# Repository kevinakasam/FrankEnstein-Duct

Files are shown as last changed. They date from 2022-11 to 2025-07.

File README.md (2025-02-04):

## Welcome to the release version of the FrankEnstein V2 Toolhead!

As the brainchild of KevinAKASam and successor to the orginal Frank toolhead, Frank 2 builds upon it's predecessor by being even more modular with support for a wide vareity of hotends and extruders for the Ender 3 and similar with its carriage plate mount as well as as any printer with a front MGN12H linear rail (with some tweaking depending on the printer). Frank 2 features double sided dual fan cooling for either 4010 or 5015 blower fans and well as the option of either 3010 or 4010 fans (with printed adapter) for hotend cooling. The entire tool head is held together securely by 4 screws to the mount and 2 from the extruder mount for easy assembly and disassembly. As in Frank 1, Frank 2 also uses standard Voron spec heat set inserts (M3x5x4) to ensure the longevity of your printed parts while assembling and dissaembling.

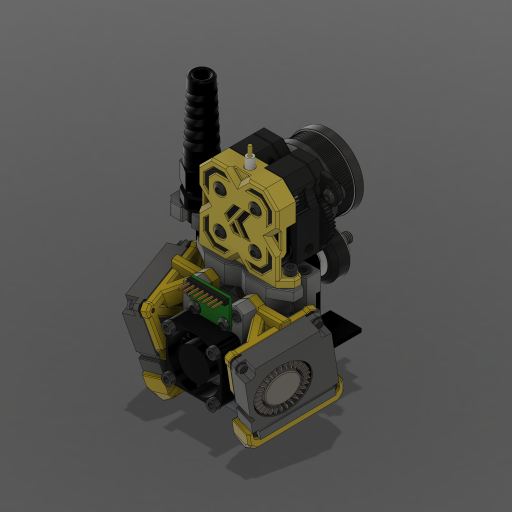
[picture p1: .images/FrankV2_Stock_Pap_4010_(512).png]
Frank V2 using the stock Ender hotend with the Papilio Lite, dual 4010 part cooling, and 3010 hotend cooling


<dl>
<dt>Supported Hotends:</dt>
<dd>Dragon</dd>
<dd>Dragonfly BMO</dd>
<dd>Dragonfly BMS (7 fin)</dd>
<dd>Spider Pro</dd>
<dd>Spider V2</dd>
<dd>Stock Ender 3 (Creality Mk8)</dd>
<dd>Triangle Labs TR6</dd>
<dd>TZ V6</dd>
<dd><em>and most hotends that use one of the above mounting patterns...</em></dd>

<dt>Supported Extruders:</dt>
<dd>Bowden</dd>
<dd>LGX Lite</dd>
<dd>Orbiter 1.5</dd>
<dd>Orbiter 2.0</dd>
<dd>Papilio</dd>
<dd>Sherpa Mini (with or without K Face)</dd>
<dd><em>and most extruders that use one of the above mounting patterns...</em></dd>
</dl>

#### Bill of Materials

| Item 					| Quantity | |
|---|---|---|
| **For Carriage Plate Base:** 					| | |
| &nbsp;&nbsp;Voron spec heatset insert 		| x6 (x7 for E3 V2 plate) | |
| &nbsp;&nbsp;M3x8 SHCS 		| x2 | |
| &nbsp;&nbsp;**For BL/CR Touch Mount:** 	| | |
| &nbsp;&nbsp;&nbsp;&nbsp;M2x8mm SHCS | x2 | |
| 					| | |
| **For MGN12H Base:** 					| | |
| &nbsp;&nbsp;300mm MGN12H Linear Rail 		| x1 | |
| &nbsp;&nbsp;Voron spec heatset insert 		| x10 | |
| &nbsp;&nbsp;M3x4mm or 5mm SHCS 		| x4 | |
| &nbsp;&nbsp;M3x35mm BHCS (preferred) or SHCS		| x2 | |
| &nbsp;&nbsp;**For Cable mount:** 		| | |
| &nbsp;&nbsp;&nbsp;&nbsp;M3x10mm SHCS | x2 | |
| &nbsp;&nbsp;**For Klack Mount:** 		| | |
| &nbsp;&nbsp;&nbsp;&nbsp;M3x6mm SHCS | x2 | |
| 					| | |
| **For Hotend Mount:** 					| | |
| &nbsp;&nbsp;Hotend of choice 		| x1 | |
| &nbsp;&nbsp;Voron spec heatset insert 		| x8 (or x10 for some hotends) | |
| &nbsp;&nbsp;Hotend mounting screws 		| Varies (Should come with hotend)| |
| &nbsp;&nbsp;M3x35mm SHCS 	 | x4 | |
| &nbsp;&nbsp;**For 3010 and 4010 Cooling:** 		| | |
| &nbsp;&nbsp;&nbsp;&nbsp;3010 or 4010 axial fan	| x1 (Ball bearing preferred)	  | |
| &nbsp;&nbsp;&nbsp;&nbsp;M3x12mm SHCS | x4 | |
| &nbsp;&nbsp;**For 4010 fan adapter:** 		| | |
| &nbsp;&nbsp;&nbsp;&nbsp;M3x8mm SHCS | x4 | |
| &nbsp;&nbsp;&nbsp;&nbsp;Voron spec heatset insert | x4 | |
| 					| | |
| **For Extruder Mount:** 					| | |
| &nbsp;&nbsp;Extruder of choice 		| x1 | |
| &nbsp;&nbsp;Voron spec heatset insert 		| x2 to x4 depending on extruder  | |
| &nbsp;&nbsp;M3x20mm SHCS or BHCS or 		| x2 (non-LGX Lite) | |
| &nbsp;&nbsp;M3x8mm SHCD or BHCS 		| x2 (LGX Lite ONLY) | |
| &nbsp;&nbsp;Extruder mounting screws 		| Varies (Mostly some amount of M3x6/8/10mms)| |
| 					| | |
| **For Part Cooling:** 					| | |
| &nbsp;&nbsp;**For Dual 4010:** 		| | |
| &nbsp;&nbsp;&nbsp;&nbsp;4010 blower fan | x2 | |
| &nbsp;&nbsp;&nbsp;&nbsp;M2x8mm SHCS | x6 | |
| &nbsp;&nbsp;&nbsp;&nbsp;M2x10mm SHCS | x2 | |
| &nbsp;&nbsp;&nbsp;&nbsp;M2 Washer | x2 | |
| &nbsp;&nbsp;**For Dual 5015:** 		| | |
| &nbsp;&nbsp;&nbsp;&nbsp;5015 blower fan | x2 | |
| &nbsp;&nbsp;&nbsp;&nbsp;Voron spec heatset insert | x6 | |
| &nbsp;&nbsp;&nbsp;&nbsp;M3x8mm SHCS | x2 | |
| &nbsp;&nbsp;&nbsp;&nbsp;M3x20mm SHCS | x4 | |
| &nbsp;&nbsp;&nbsp;&nbsp;M3 Washer | x4 | |

#### Print Settings: The Magic 5

```
Infill:
* 55%
Walls/Perimeters:
* 5
Top Layers:
* 5
Bottom Layers:
* 5
```

Not finding exactly what you need? Check out [User Mods](./User_Mods) to see if it's been made or if it hasn't feel free to design it and request a pull in User Mods!

Have a question or just want to hang out with some cool people? [Join our discord here!](https://discord.gg/xqpKrxt9FC)

_Build guide coming..._

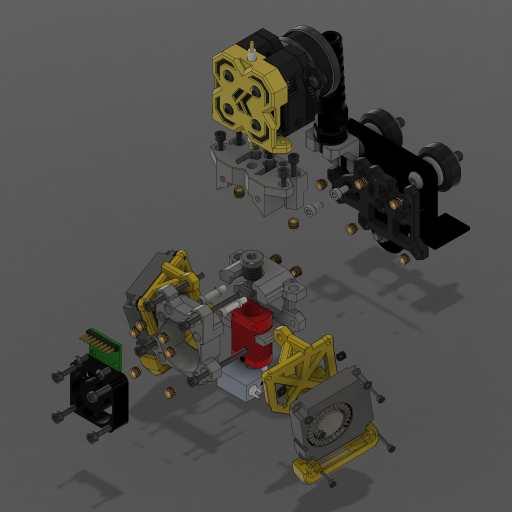
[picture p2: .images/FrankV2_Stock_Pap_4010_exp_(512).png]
An exploded view of the above Frank


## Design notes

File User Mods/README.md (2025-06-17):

# User Mods

This repository is to share your Mods (Mods of my Mods are called Mods in the following). You can add them by submitting a pull request.
All my Mods have a sperate folder, that may include further subfolders, please sort your content as described below:

## Table structure

*Thanks to the [Voron_User](https://github.com/VoronDesign/VoronUsers) Repo for this table schematic! 
Update the following table with the information about your mod:
- Your name
- A link to your sub-folder
- A short description of your mod

like so:
`
| Creator | [Mod title](link) | Description | :x: | :x: |`

| Creator | Mod title | Description |
| --- | --- | --- |
| adamstorm | [Filament Sensor](<./adamstorm/Filament Sensor>)| A simple filament sensor in the extruder mount for Papilio/Sherpa mounting pattern extruders |
| | [Camera Mount](<./adamstorm/Camera Mount>)| Add a nozzle camera to your Ender! |
|			| [Sprite Extruder Mount](<./adamstorm/Sprite Extruder Mount>)| Extruder mount for the Creality Sprite extruder |
| wight554 | [2510 Fan Dragon Mount](<./wight554/2510 Fan Dragon Mount>)| Hotend mount using 2510 fan for Dragon mount hotends |
| | [5015 HF Ducts](<./wight554/5015 HF Ducts>)| 5015 fan ducts for "HF sized" hotends |
| | [5015 UHF Ducts](<./wight554/5015 UHF Ducts>)| 5015 fan ducts for "UHF sized" hotends |
| | [Extruder Mounts](<./wight554/Extruder Mounts>)| A bunch of alternative extruder mounts |
| | [Klack HF](<./wight554/Klack HF>)| Klack dock and mount for "HF sized" hotends |
| | [Klack UHF](<./wight554/Klack UHF>)| Klack dock and mount for "UHF sized" hotends |
| | [PG7 Mount](<./wight554/PG7 Mount>)| PG7 Mount that's designed to be a bit more rigid |
| n4t3y | [AIO 5015 Duct](<./n4t3y/AIO 5015 Ducts>) | A mount for the 5015 fans with integrated duct instead of separately fixed |
| | [AIO 5015 LED Duct](<./n4t3y/AIO 5015 LED Ducts>) | A mount for the 5015 fans with integrated duct and LED Mount instead of separately fixed |
| SampleMan | [Sample](./SampleMan/Sample) | This is a sample entry |

## How to create a pull request 

1. Create a fork of the repository
    - You can find a Button labeled `Fork` at the top right. Clinking on that creates a copy aka fork of this respository in your GitHub account.

2. Create a new folder
    - Navigate into the Mod folder you want to upload your Mod to.
    - Click on `Add file` -> `Create new file`. Then type `YourNickname/YourModName/README.md` to create your folder (click on `commit new file`).
    - If you plan to upload more than one Mod, add simply add more subfolders in your folder like `YourNickname/YourFirstModName/README.md` and `YourNickname/YourSecondModName/README.md` and so on. 
    - Please use short folder names.

3. Edit README and add your files
    - Click on the README.md and then on the pencil on the right top/center to edit the README. Add all required information as described below.
    - Click on `Add file` -> `Upload files` to upload all your Mod files.
    - The stock title of a commit is `Add files via upload` replace that with the title of your Mod.

4. Edit the main README.md of the Mod
    - Navigate back to the Mod folder you made your Mod for. Edit this file and add your mod to the alphabetic table by adding a new line with `| Creator | [Mod title](link) | Description | | :x: | :x: |`
    - The `link` for the `[Mod title](link)` should look like that: `./YourNickname/YourModName` just like you did above
    - Example: `| KevinAkaSam | [Modifius](./KevinAkaSam/Modifius) | Modifius adds ...  | :grey_question: | :grey_question: |`
    - Note `Modifius` is just an idea, yours may be called `Adaption to bearing size xy`

5. Submit the Pull Request
    - Navigate back to this repository (not the one you forked) and click on `Pull requests` next to `<> Code` `© Issues`
    - Click on the green square on the right `New pull request`
    - A new dialog/window opens and starts with:
        >Compare changes
        >
        >Compare changes across branches, commits, tags, and more below. If you need to, you can also `compare across forks`.
    - Click on the `compare across forks` and at the line below select your forked respository as `head respository`
    - Add you Mod name as title of the pull request, add the information to the form and click on  `Create Pull Request` at the very end.
    - If you did anything right we will merge your pull request :)
 
## Create a folder

To add your work create a folder that has the following structure:

    - Main repository `User-Mods` 
        - Nickname Subfolder eg. `KevinAkaSam`
            - Modname Subfolder eg. `Modifius`
            - Modname Subfolder eg. `Modimedi`
        - Nickname Subfolder eg. `hawk16zz`
            - Modname Subfolder eg. `Mod_A`
            - Modname Subfolder eg. `Mod_B`

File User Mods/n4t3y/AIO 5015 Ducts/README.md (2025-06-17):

This mod combines the 5015 holder and duct into a single piece to aid with duct drooping and fitment to the fan, while also removing a heat insert and bolt which would otherwise be needed for attaching the duct to the mount. An integrated wedge support piece is included to remove the need for adding slicer generated supports.

The model is fully printable without supports, although the top side of the duct can come out stringy but will still work fine after removing the hanging filament.

The LHS is the base printable file and to print the RHS, the mount and bracket should be mirrored in the slicer.

The mount is designed to be oriented in the slicer like this (grey element is integrated support):

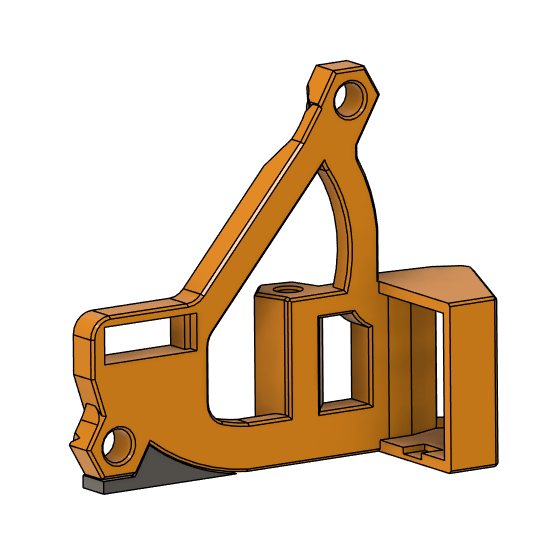
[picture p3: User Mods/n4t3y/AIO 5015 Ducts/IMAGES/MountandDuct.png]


The bracket is held in place with a notch integrated into the mount, as well as the fan when it is installed, so there is no need for any additional hardware.

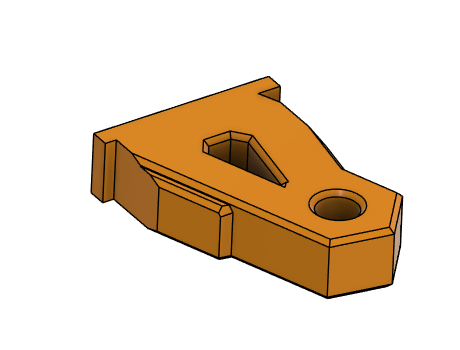
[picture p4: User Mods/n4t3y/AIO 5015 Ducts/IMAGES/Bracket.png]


The bracket should slide easily into the slot in the mount (take note of orientation of bracket in the mount):

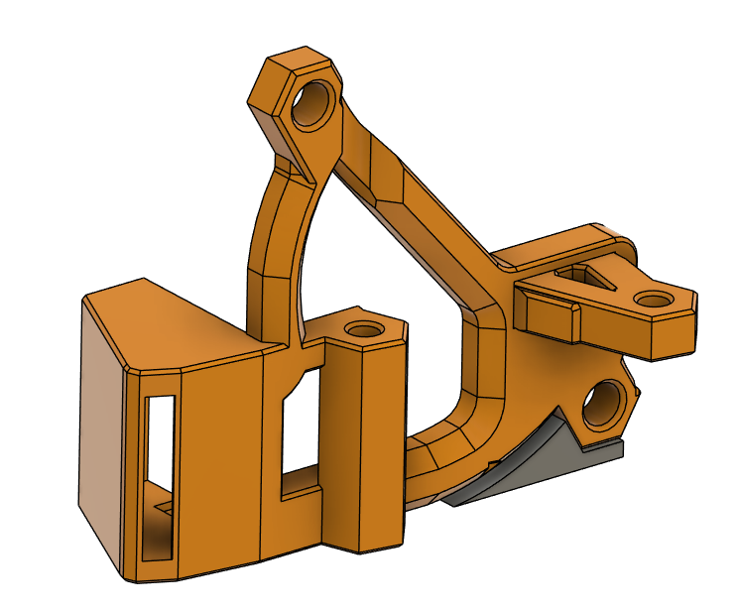
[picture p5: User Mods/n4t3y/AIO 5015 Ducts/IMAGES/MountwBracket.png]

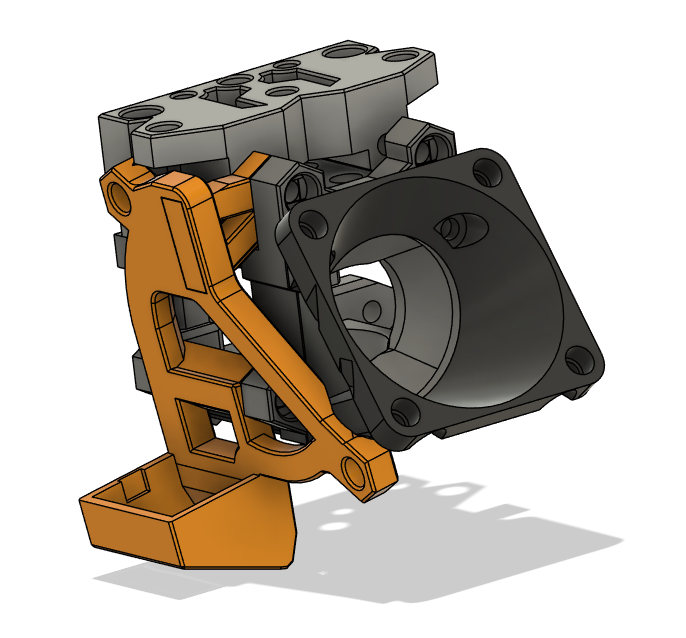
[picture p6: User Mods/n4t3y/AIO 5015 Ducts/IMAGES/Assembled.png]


The additional material around the bracket may intrude a bit on the intake of the fan on the right hand side, but not a significant amount more than the original holder.

Original Holder:

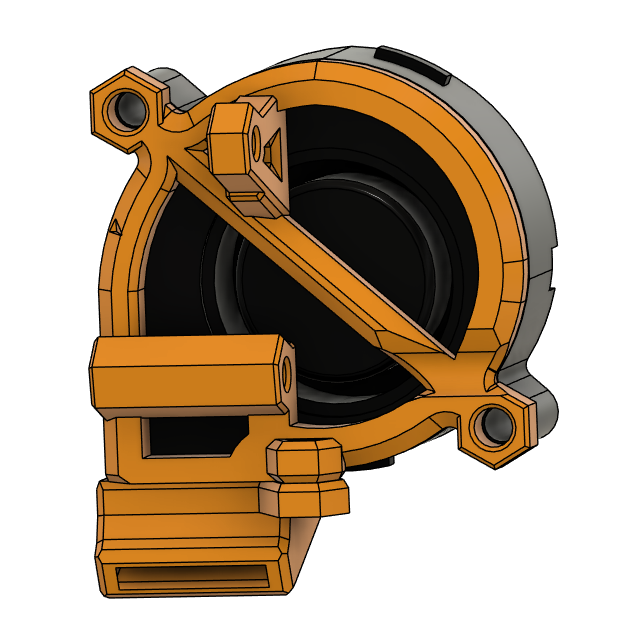
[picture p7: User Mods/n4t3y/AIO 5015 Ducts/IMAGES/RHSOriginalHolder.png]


AIO Mount:

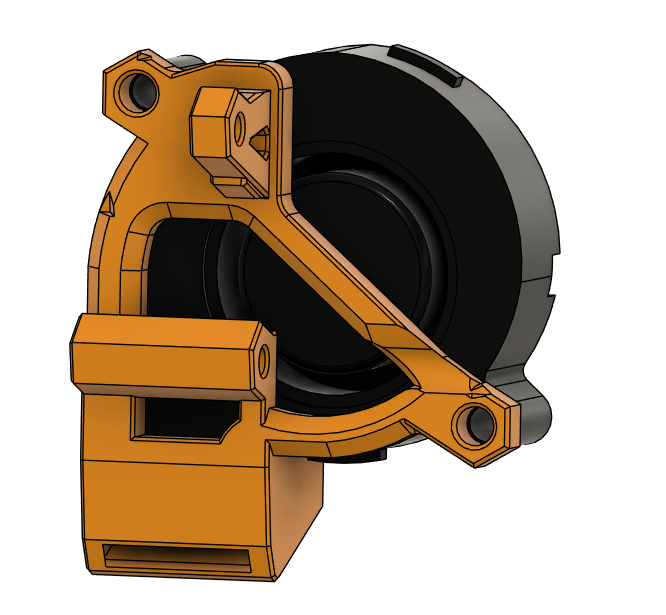
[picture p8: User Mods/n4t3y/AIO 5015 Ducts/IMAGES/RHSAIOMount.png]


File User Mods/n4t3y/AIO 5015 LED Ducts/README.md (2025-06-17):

This mod adds LED holders to the AIO 5015 duct. It is compatible with the same wedge support in the base duct.

The model is fully printable without supports, although the top side of the duct can come out stringy but will still work fine after removing the hanging filament.

The LHS is the base printable file and to print the RHS, the mount and bracket should be mirrored in the slicer.

Orientation is the same as the base AIO Duct. Refer to the base AIO instructions [here](../AIO%205015%20Ducts/README.md) for printing instructions.

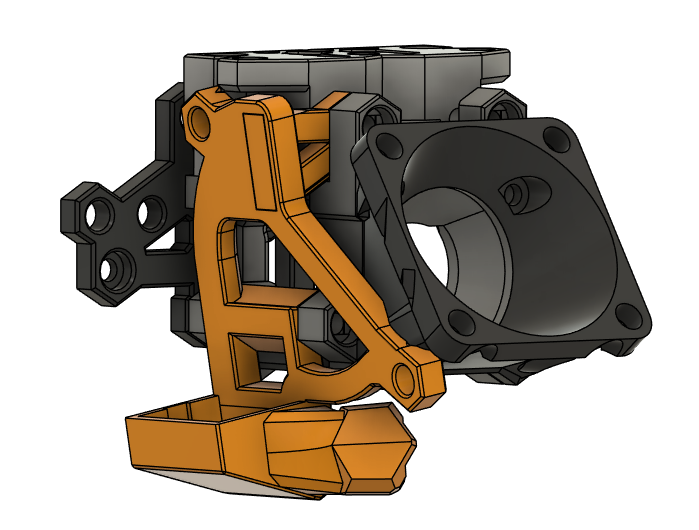
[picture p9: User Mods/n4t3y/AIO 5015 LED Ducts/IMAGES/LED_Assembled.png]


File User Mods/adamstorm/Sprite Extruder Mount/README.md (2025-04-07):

The Creality Sprite Extruder is a common upgrade/stock option that many Ender users have. While there are better extruders out there, it is a capable extruder. Just a little heavy. I don't judge ;-) 

In the interest of working with what you have, I created this mount. The Sprite extruder was the first upgrade I made on my Ender, but I quickly found that I wanted to upgrade the part cooling capability. Frank fit the bill but didn't support my only DD extruder at the time. 

STL is oriented for proper printing, no supports needed. CAD is included for your remixing pleasure. 

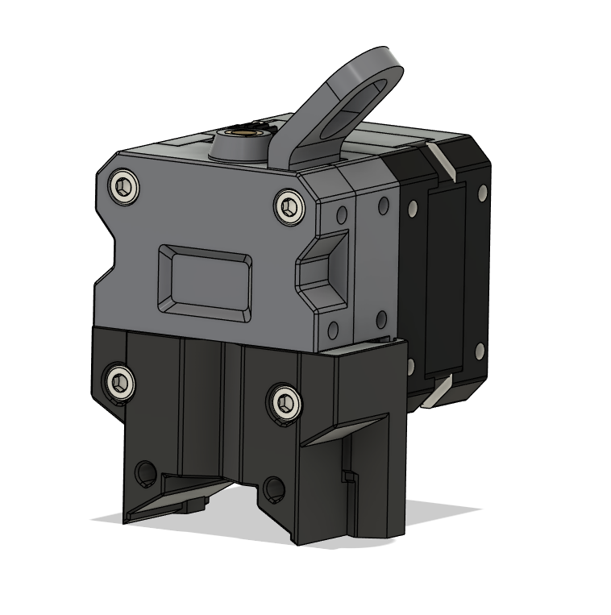
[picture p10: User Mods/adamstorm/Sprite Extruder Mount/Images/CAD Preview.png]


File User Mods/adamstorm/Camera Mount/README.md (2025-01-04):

Add a nozzle camera to your Ender!
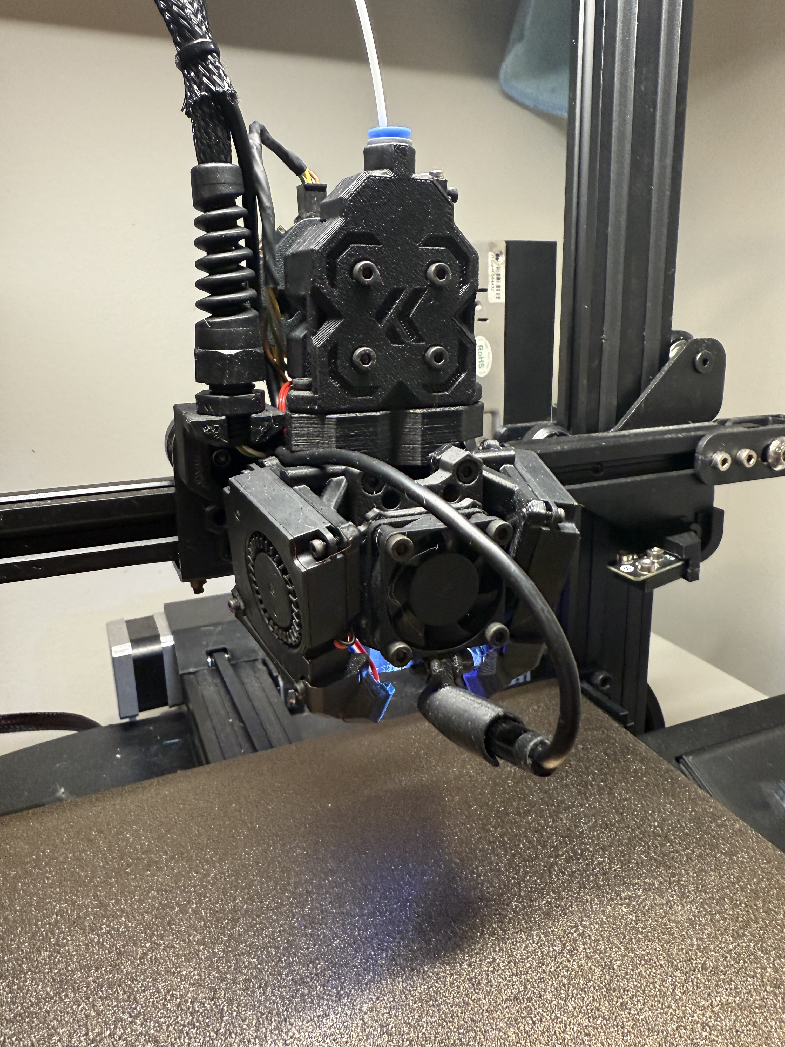
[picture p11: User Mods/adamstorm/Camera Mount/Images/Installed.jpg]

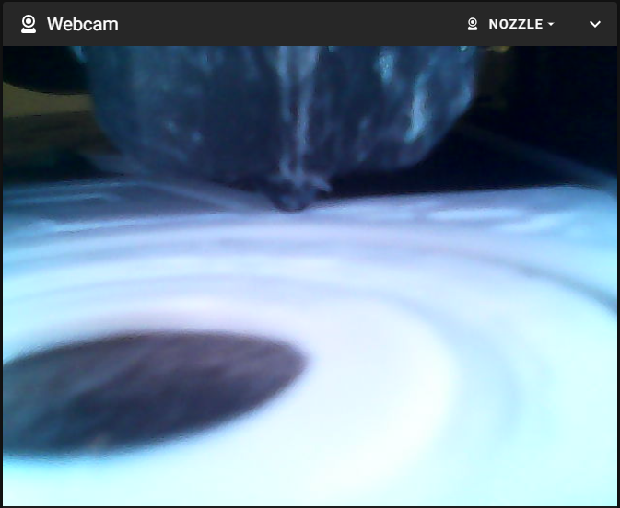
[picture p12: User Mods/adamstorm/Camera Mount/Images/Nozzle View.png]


I picked up a cheap endoscope off Temu and needed a way to mount it. This is a plate that is sandwiched between the hotend mount and 3010 fan or 4010 adapter. It gives a simple mounting point to add your favorite accessory. All you need is an M3 bolt and M3 nut. The screws that mount your 3010 fan or 4010 adapter might need to be a tad bit longer.

The included camera mount is for an endoscope that is 7.4mm in diameter. It is held in with a friction fit, the cutout portion allows for tight fit by flexing to accomodate the camera. CAD file is included if you want to modify for other size camera or other accessory.

STLs are oriented for how I printed the parts. For strength, I printed the camera mount on it's end. It printed fine for me, but it does have a small bed contact area so it might test your bed adhesion. I can see some setups would need to enable a brim in the slicer, but it did print successfully for me without. YMMV.

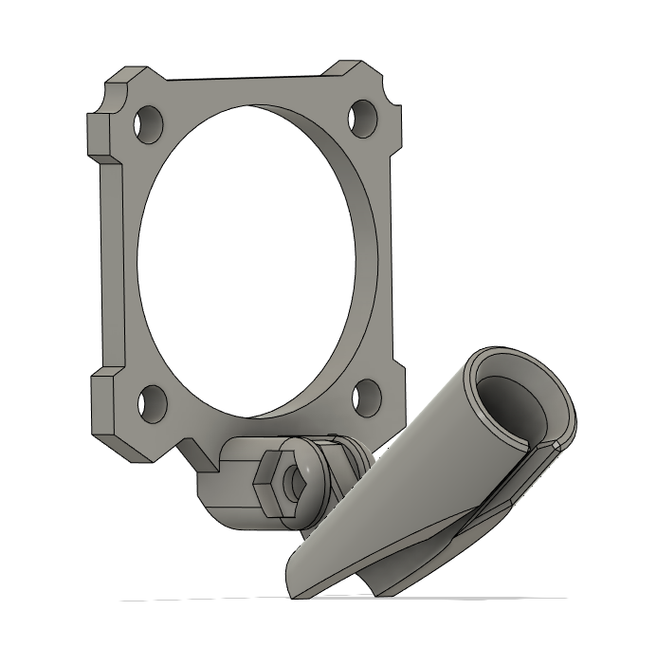
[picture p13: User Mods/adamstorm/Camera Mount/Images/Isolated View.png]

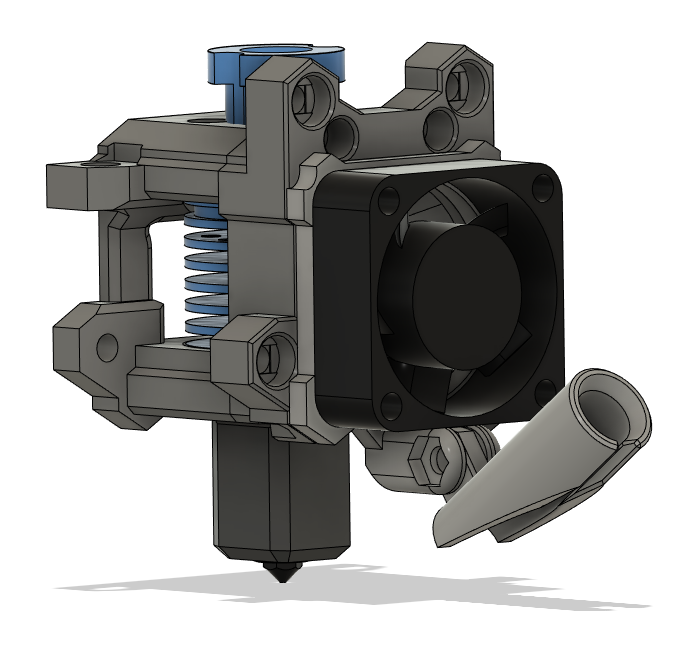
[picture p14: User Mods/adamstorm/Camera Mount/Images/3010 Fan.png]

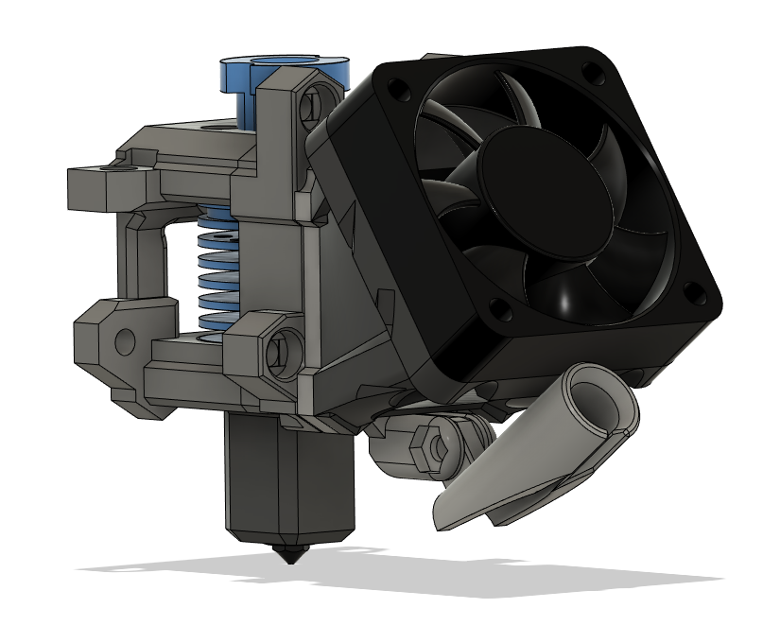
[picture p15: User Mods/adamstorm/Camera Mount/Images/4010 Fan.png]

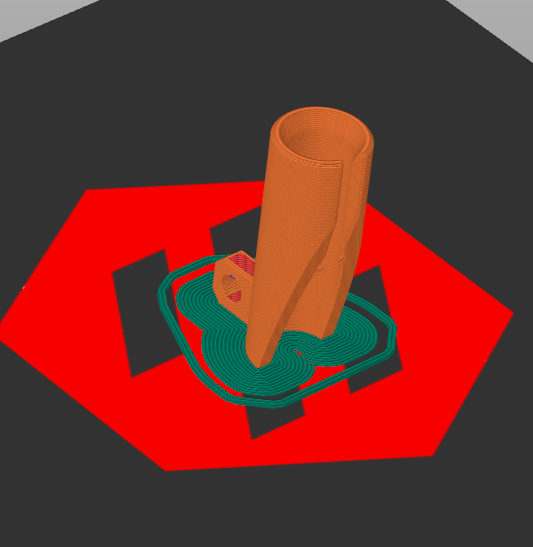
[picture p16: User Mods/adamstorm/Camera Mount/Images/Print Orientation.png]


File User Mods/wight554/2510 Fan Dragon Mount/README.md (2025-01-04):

## 2510 Fan Mount for Dragon mount hotends

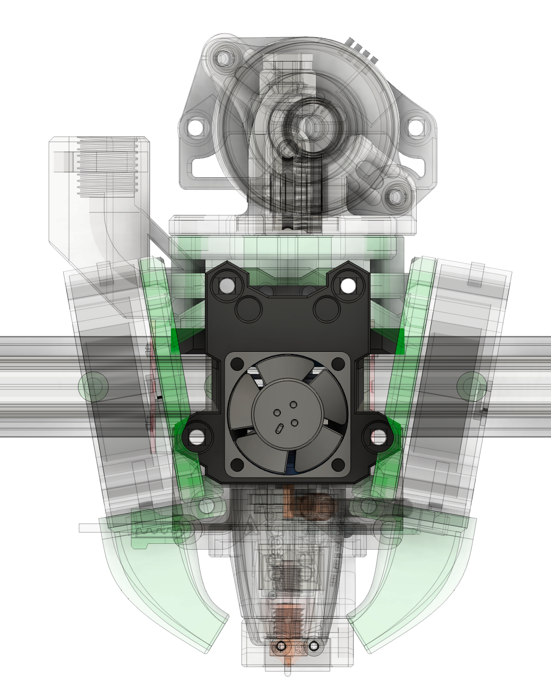
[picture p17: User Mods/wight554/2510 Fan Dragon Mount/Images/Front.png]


### Description

2510 tend to be less prone to clog on Dragons and similar hotends, so it's a nice upgrade to have on Frank

### BOM

- 4x M2.5X14mm screws (16mm should work too)
- 2510 Fan (Delta Electronics 5v ASB02505SHA-AY6B preferred)

### Assembly

Should be the same as 3010 version, I made assembly somewhat easier but it should be straightforward anyway.

### Delta 5v installation guide (for EBB36/42) borrowed from Replimat labs:

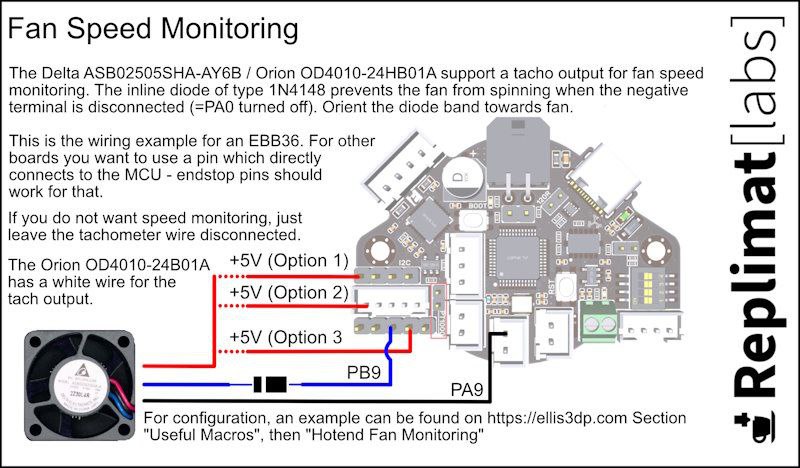
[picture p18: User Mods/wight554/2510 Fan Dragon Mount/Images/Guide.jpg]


### Other Images:

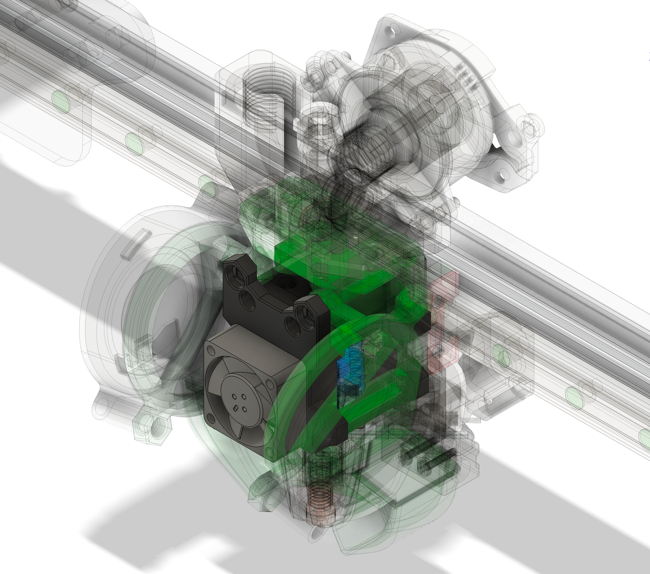
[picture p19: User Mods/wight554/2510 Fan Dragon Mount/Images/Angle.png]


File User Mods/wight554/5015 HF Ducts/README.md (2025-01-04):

## 5015 HF Ducts

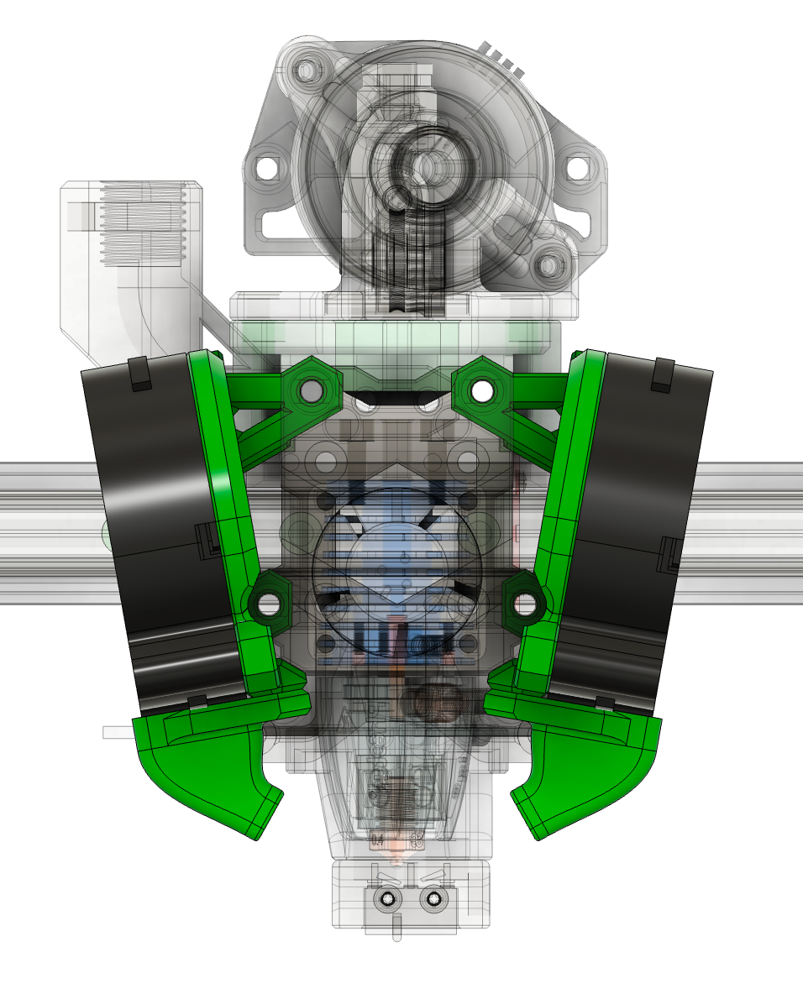
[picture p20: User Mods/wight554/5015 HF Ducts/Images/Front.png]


### Description

Longer ducts inspired by LH Stinger to work with volcano (or 8.5mm longer) versions of supported hotends and others, like Rapido HF

### BOM

The same as normal ducts

### Assembly

The same as normal ducts

### Other Images:

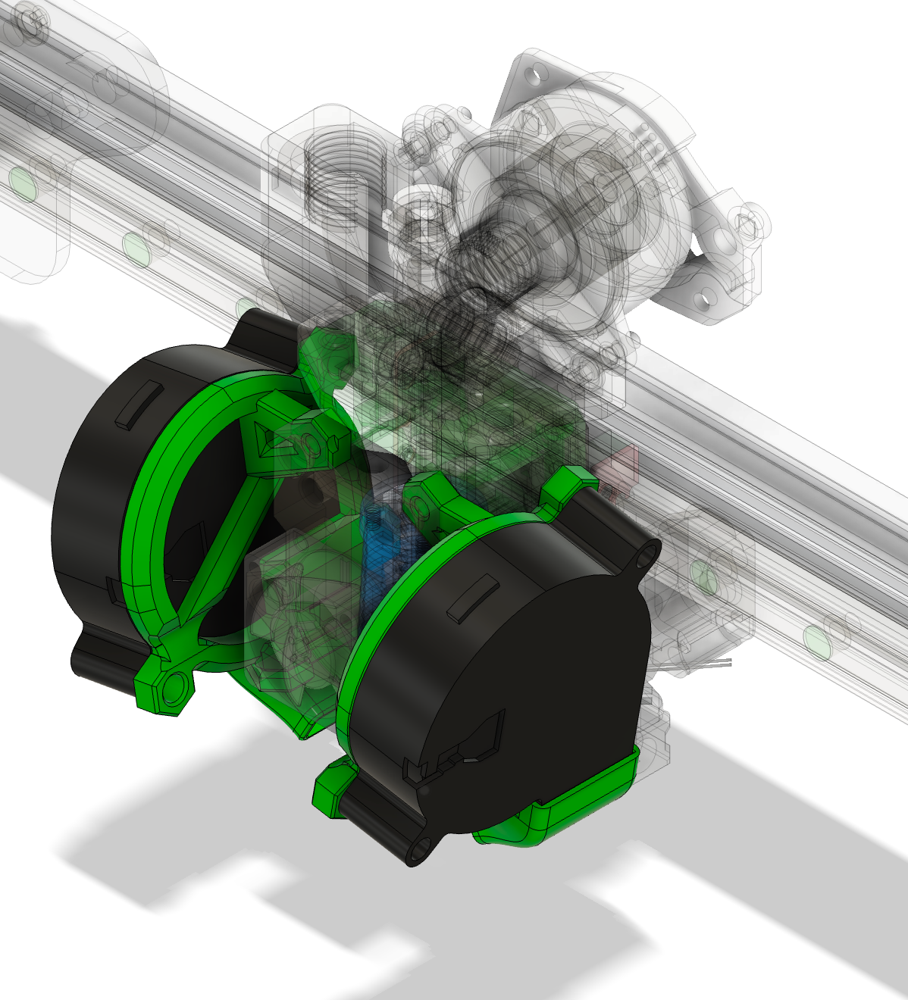
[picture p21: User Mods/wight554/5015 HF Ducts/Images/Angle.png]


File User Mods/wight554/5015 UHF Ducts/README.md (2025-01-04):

## 5015 UHF Ducts

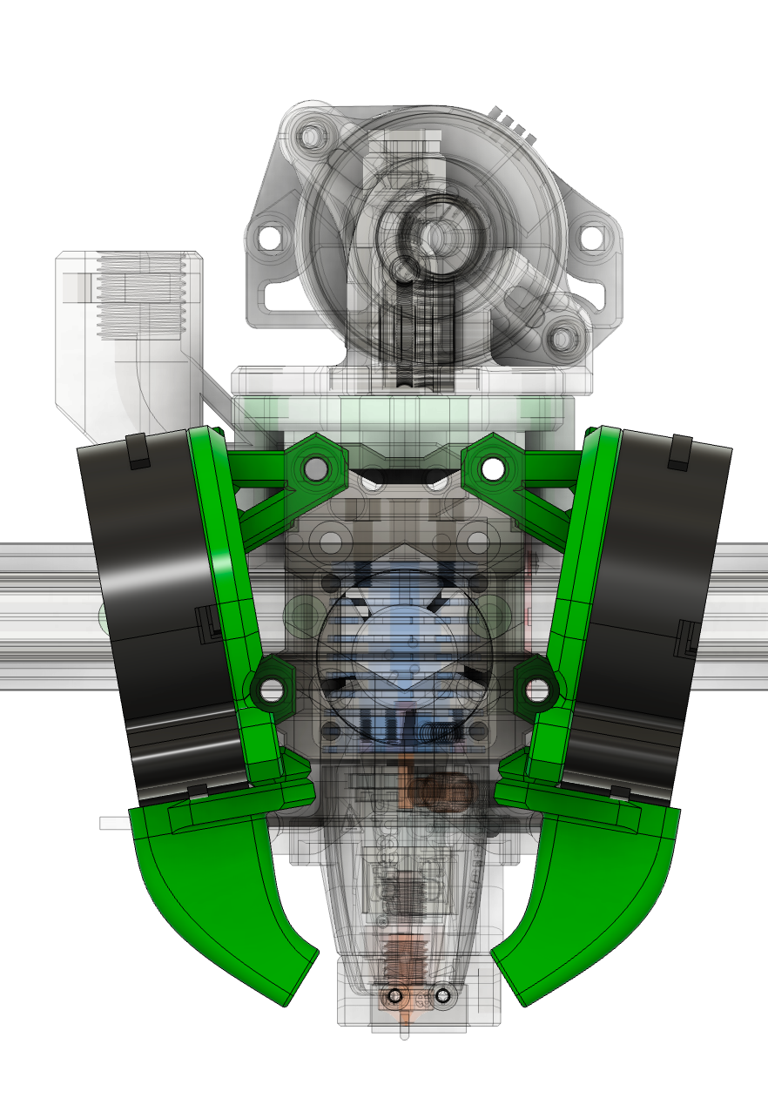
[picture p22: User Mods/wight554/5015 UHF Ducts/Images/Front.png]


### Description

Longer ducts inspired by LH Stinger to work with supported hotends with long meltzone (17mm longer than Dragon and similar) and others, like Rapido UHF

### BOM

The same as normal ducts

### Assembly

The same as normal ducts

### Other Images:

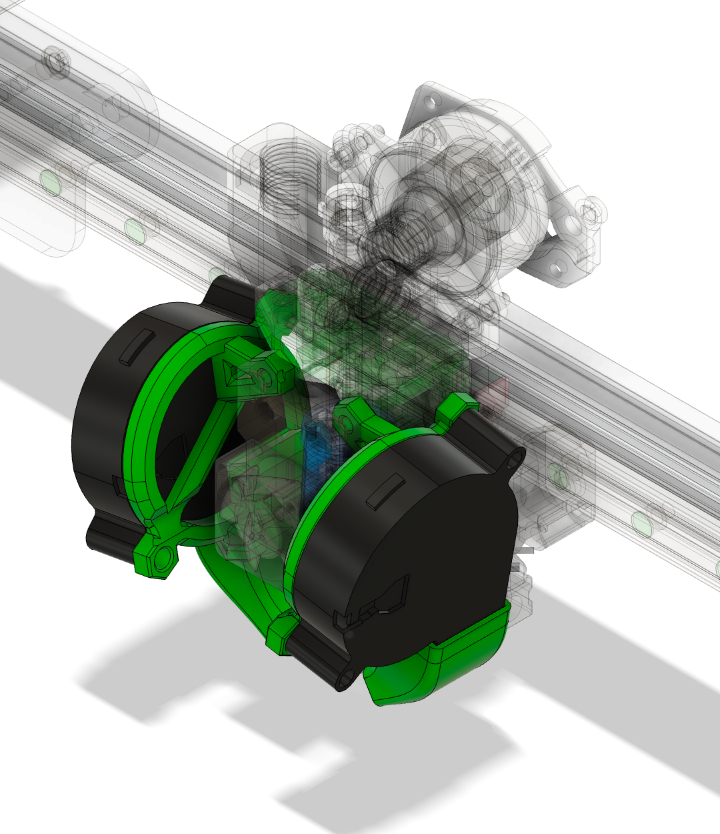
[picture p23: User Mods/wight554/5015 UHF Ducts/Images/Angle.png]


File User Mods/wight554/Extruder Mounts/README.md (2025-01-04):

## Extruder Mounts

### Description

Assortment of extruder mounts I made with some minor improvements:

- LowBoi (Orbiter mount)
- Papilio Lite (3 screw, alternative mount using a nut at rear)
- WWMBG (Orbiter mount)
- Protoxtruder 2

### BOM

Same as normal, except M3 Hexnut for Papilio Lite mount

### Printing

Designed to be printed laying on this face:
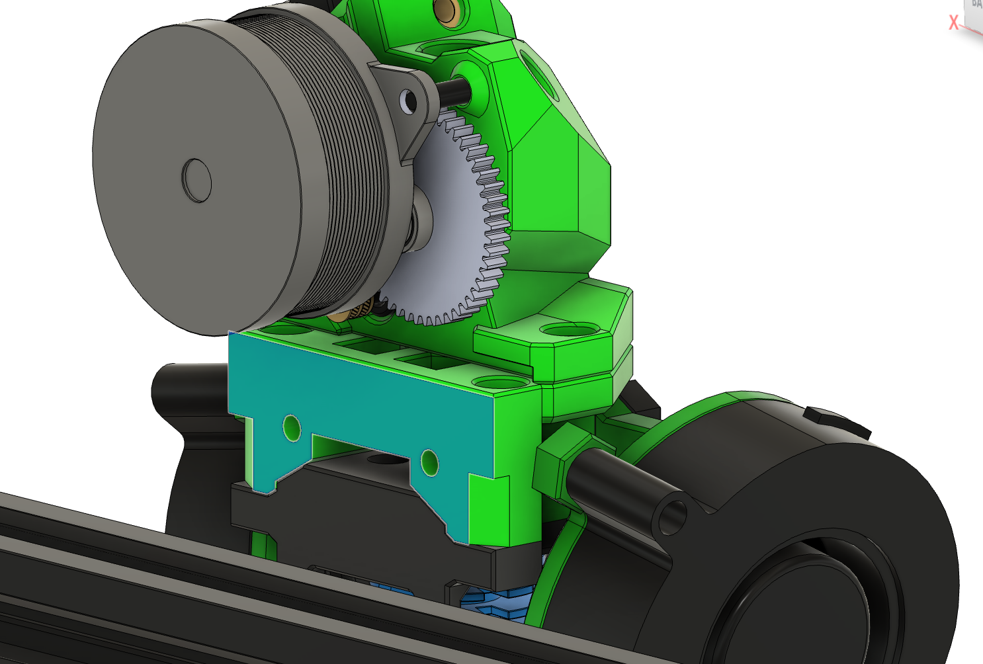
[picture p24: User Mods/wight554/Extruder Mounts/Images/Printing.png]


### Assembly

The same as normal mounts

### Images:

#### LowBoi
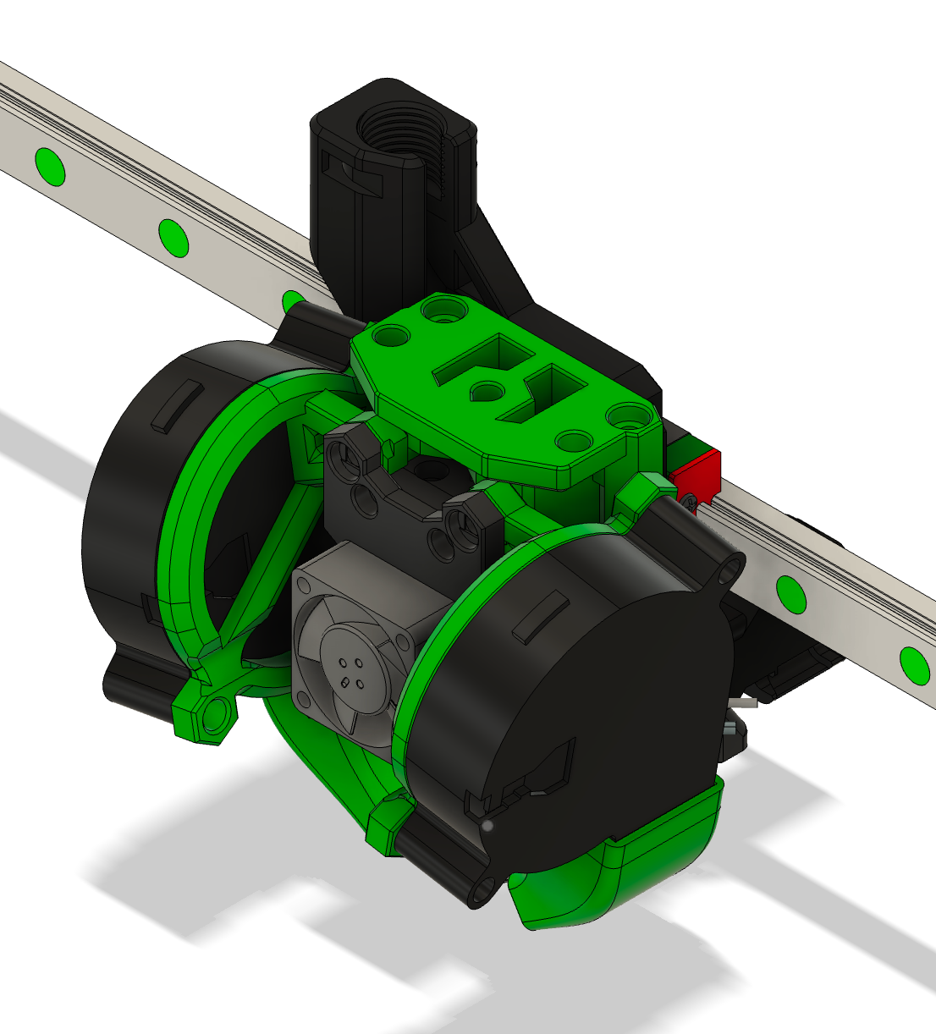
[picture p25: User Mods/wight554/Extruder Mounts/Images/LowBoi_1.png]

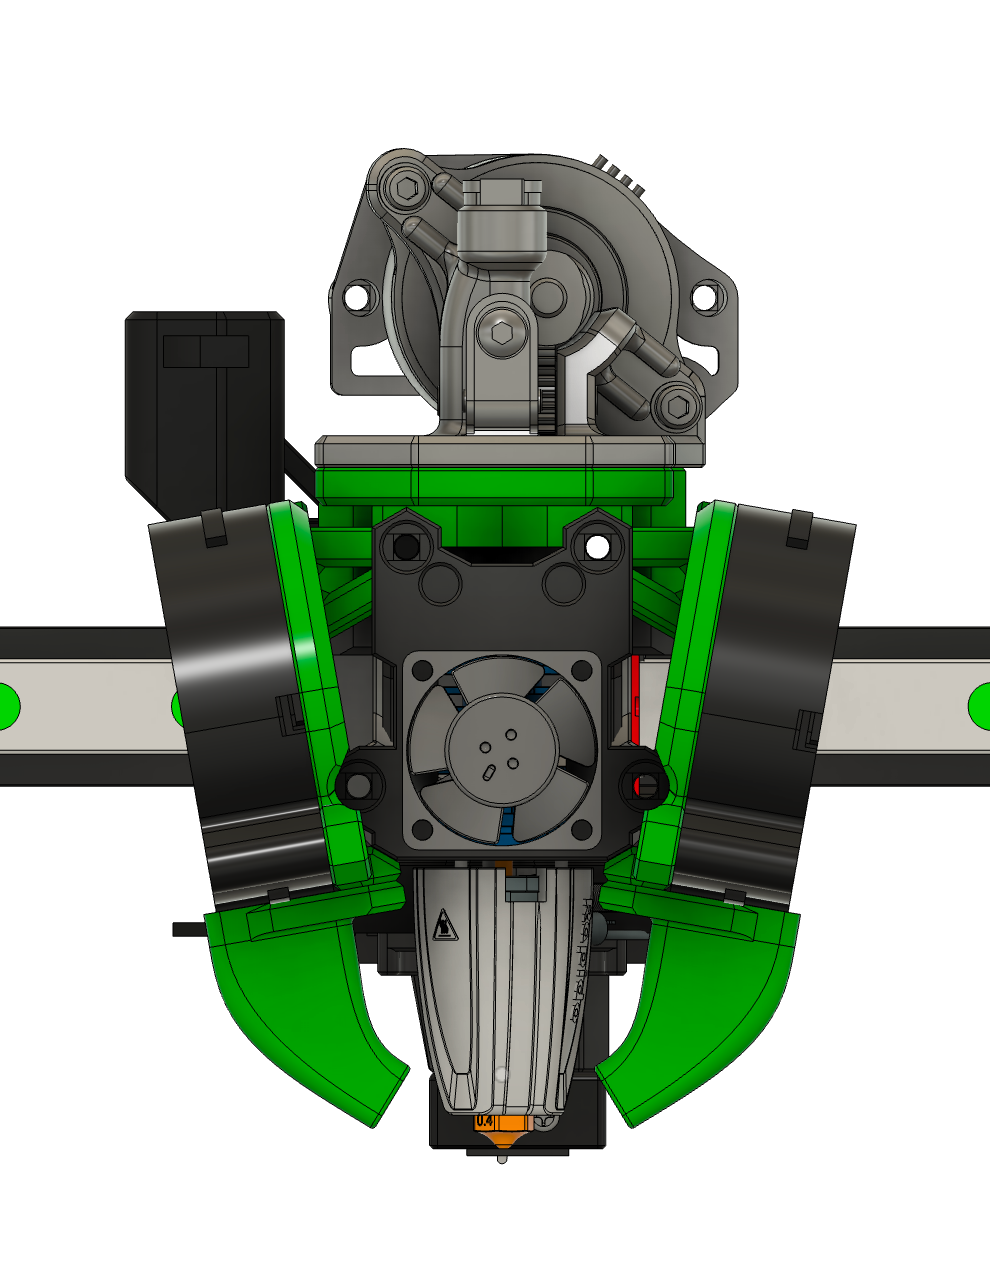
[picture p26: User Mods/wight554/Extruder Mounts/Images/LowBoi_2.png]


#### Papilio Lite



#### WWMBG



#### Protoxtruder



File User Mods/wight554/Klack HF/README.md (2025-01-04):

## Klack HF



### Description

Klack dock and mount (for MGN12H carriage) designed to work with HF ducts. Shoukd to be used with Klack R2.2 

### BOM

The same as normal dock and mount

### Assembly

The same as normal dock and mount

### Other Images:



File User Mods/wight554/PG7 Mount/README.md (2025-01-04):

## PG7 Mount



### Description

Stiffer version of PG7 Mount. It has some room for wiring and allows fixing thread with a tie

### BOM

- PG7 Cable Gland

### Assembly

Insert cable to gland, screw the gland onto mount

### Other Images:



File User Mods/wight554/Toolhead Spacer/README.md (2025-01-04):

## Toolhead spacer



### Description

5mm spacer for MGN12H carriage mounting. Useful when you can sacrifice some Y (or have extra space) and want to use longer extruder with toolhead board (e.g. G2SA, Orbiter, LowBoi etc)

### BOM

- 4x M3x40mm (5mm longer than original BOM)

### Assembly

Slap it onto hotend mount at rear side and mount whole assembly onto carriage

### Other Images:



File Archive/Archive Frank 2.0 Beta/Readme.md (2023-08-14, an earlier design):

### Frank 2.0 BETA

Please join the Discord and the Beta channel to read more about this!

This folder is to store all the Beta files, do not print this without the information from the Beta channel!

#### Updates

14.08.2023: Finally another update
- Fixed the 5015 and hotendmount overlap (Thanks hawk16zz)
- Fixed the BL Touch Mount and hotendmount overlap (Thanks hawk16zz)
- Bl-Touch Mount should now be also compatible with the CR-Touch
- Added 5015 LED Ducts
- Added a new 4010 Adapter with an included ADXL Mount since the ones in the hotend mount are blocked with the adapter (Thanks Takus)

16.07.2023
- Fixed an overhang issue with the back of the Dragon, Stock and TR6 hotend mounts and the part cooling fan holders
- Added 5015 fan support (dual setup, single fan and LED Duct will be added later)
- Added Rapido UHF, this will be improved soon, maybe wait printing this but it works
- Extruder mounts are splitted in normal and highflow. Aside the Rapido every hotend uses the normal ones

09.07.2023
- Fixed an overhang issue with the back of the hotend mounts 

07.07.2023
- Added a mount for the Phaetus Dragongly BMO
- Added a mount for the Sherpa Mini with the K-Mount
- Modified the left 4010 holder to fit the Sherpa Mini K-Mount

05.07.2023: BL-Touch, stock MK8 hotend, LGX Lite and ADXL
- Added a mount to use a BL Touch (the holes on the plate can also be use used to use a permamntly mounted hidden ADXL)
- Added a mount for the stock MK8 hotend
- Added a mount for the LGX Lite
- Added a mount for an ADXL sensor - these mount to the front part of the Hotend mount, so you will have to reprint that part to use it

02.07.2023: Overlap fix + Dragon
- Fixed the little overlap between the extruder mounts and the hotendmounts on the rear screw point
- Added a mount for the Phaetus Dragon

26.06: I made an oopsie + BMS7 fin
- My mistake, I made a mistake with the basic layout of the first design so the stock hotend and 1:1 replacements won't fit (I used the 6 fin BMS as a reference and not the 7 fin BMS). This means that all the parts except the duct will not fit and will have to be reprinted if you have already printed them (I don't think anyone has done that, but just in case) (okay Andy - I'm sorry)
- Added a mount for the BMS fin

#### Draft BOM

A very Draft BOM, which gives you a rough estimation of parts you need:

##### Common
- 8x M3 heat insert (3x5x4mm - standard ones)
- 4x M3x35mm screw (main screws that hold everything together and to the plate)
- 2x M3x18mm (can be also 16mm or 20mm long, these are to mount the extruder mount to the assembly)
- 4x M3x12mm (to mount the 3010 fan, if you want to use a 4010, you need extra 4x M3x8mm to mount the adapter)
- 2x M3x6mm (can be also 8mm, maybe even 10mm long - these are to munt the backplate to the x axis metal plate)
- Plus the screws you need to mount the extruder to the extruder mount
- Plus the screws you need to mount the hotend to the hotend mount

##### 4010 Blower (Partcooling)

8x M2x8mm

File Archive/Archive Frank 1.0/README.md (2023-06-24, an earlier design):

# FrankEnstein-Duct
*Frankenstein also known as Frank Enstein is a light weight fanduct for the Ender 3 or similar printers (Not the E3 V2!). It adds a 5015 blower fan and is also compatible with a wide range of Hotends and Extruders.*

**Frank 2.0 will be reeased soon! Maybe you want to wait with printing till then. Join the Discord for more information**

### Don't we have enough fan ducts for the Ender 3? Yet another one...?

Yes, another one! And I'll tell you why. Frank is also known as Frankenstein because it's not beautiful or aesthetic (I like the look a lot, though), but is reduced to sheer fun. There is no plastic that is not really necessary. This makes Frank very lightweight, but also quick to print and easy to repair. The simplicity of the duct allows for a very wide range of hotends and extruders, as there is no plastic to get in the way. With only 4 printed parts you get a new powerful duct for your Ender 3! (Not the E3 V2!)

 

---

### Supported Hotends, Extruders and additional Hardware

This section lists all compatible Hotends and Extruder. If you're missing your hotend or extruder, feel free to post a request for that on my Discord. Let us create the first Fan Duct, that support <i>almost*</i> **everything**! (*Please not the Limitations section below)

#### Hotends
    1.  Stock Mk8 
    2.  Phaetus - Dragonfly BMS     (6 anf 7 fin version (see below))
    3.  Phaetus - Dragonfly BMO     (with V6 mount, rigid mount will be added soon)
    4.  Phaetus - Dragon            (Standard Flow and High Flow)
    5.  Phaetus - Dropeffect XG
    6.  Phaetus - Rapido HF/UHF     (not public yet but available on my Discord)
    7.  E3D - V6
    8.  E3D - V6 Vulcano
    9.  E3D - Revo 6
    10.  E3D - Revo Micro
    11. E3D - Revo Voron
    12. Haldis - Red Lizard         (with stock version)
    13. Creality - Spider Hotend    (with BMS 7 version)
    
Hotends links: [Dragonfly BMS](https://www.phaetus.com/dragonfly-bms/), [Dragonfly BMO](https://www.phaetus.com/dragonfly-bmo/), [Dragon](https://www.phaetus.com/dragon-st/), [Dropeffect XG](https://dropeffect.phaetus.com/products/xg-hotend), [V6](https://e3d-online.com/products/v6-all-metal-hotend), [V6 Vulcano](https://e3d-online.com/products/volcano-hotend), [Revo 6](https://e3d-online.com/products/revo-six), [Revo Micro](https://e3d-online.com/products/revo-micro), [Revo Voron](https://e3d-online.com/products/revo-voron), [Red Lizard](https://aliexpress.com/item/1005003366657998.html)

#### Extruders
    1. Bowden extruders             (stock or any replacement you're using)
    2. Annex's - Sherpa Mini        (With adapter also Sherpa Micro)
    3. Róbert's - Orbiter V2.0
    4. Bondtech - LGX Lite
    5. Triangelab - TBG Lite

Extruder links: [Sherpa Mini](https://www.https://github.com/Annex-Engineering/Sherpa_Mini-Extruder), [Sherpa Micro](https://github.com/Annex-Engineering/Sherpa_Micro-Extruder), [Orbiter V2.0](https://www.https://orbiterprojects.com/orbiter-v2-0/), [LGX Lite](https://www.bondtech.se/product/lgx-lite-large-gears-extruder/), [TBG Lite](https://www.aliexpress.com/item/1005003908281100.html)

#### Hardware
    1. BL-Touch and Clones
    2. ADXL345-Accelerometer (for Klipper and RepRap) 

Hardware links: [BL-Touch](https://www.antclabs.com/bltouch-v3), [ADXL345 Sensor (Klipper)](https://www.klipper3d.org/Measuring_Resonances.html)

---

### Bill of Material: Hardware you need
<table>
    <tr>
        <td>Component</td>
        <td>Quantitiy</td>
        <td>Reuse from Printer</td>
        <td>Notes</td>
    </tr>
    <tr>
        <td>5015 Blower fan</td>
        <td>1</td>
        <td>No</td>
        <td>For ABS machines Winsinn works okay. Otherwise consider Delta, Sunon or Gdstime. </td>
    </tr>
    <tr>
        <td>4010 Axial Fan</td>
        <td>1</td>
        <td>Yes</td>
        <td>You can reuse the stock fan. You can also use 4020 fans, that's up to your preference.</td>
    </tr>
    <tr>
        <td>M3x16mm</td>
        <td>4</td>
        <td>No</td>
        <td>To mount the 4010 and the fanguide to the 4010</td>
    </tr>
    <tr>
        <td>M3x18mm</td>
        <td>2</td>
        <td>No</td>
        <td>To mount the 5015.</td>
    </tr>
    <tr>
        <td>M3x12mm</td>
        <td>2</td>
        <td>No</td>
        <td>To mount the Cable Clip. BL-Touch mount needs M3x16mm.</td>
    </tr>
    <tr>
        <td>M3x8mm</td>
        <td>2</td>
        <td>Yes/No</td>
        <td>To mount the 5015 holder. The stock ones have only a very few mm to grab, 8mm is better.</td>
    </tr>
    <tr>
        <td>M3x5x4mm heat inserts</td>
        <td>10</td>
        <td>No</td>
        <td></td>
    </tr>
</table>

---

### STL's (3mf) you need:
The STL folder has 3 sub folders which stores the files you need to build this duct:
    - **CommonAll**: Printed Parts that are common with all configurations. Currently this is only the BL-Touch mount.
    - **Hotend**:    Each hotend has it own folder, just pick the files for your hotend.
    - **Extruder**:  Just pick the extruder you want to use and then the hotend. 
You should end up with a Duct, a 5015 holder (+ clamp for V6) and a fan guide. The LGX Lite and the TBG Lite also add a sperate mount, same for the BL-Touch.
**Print settings: 55% Infill, 5 Walls,Tops and Bottoms**

#### Extras
The Extras folder contain some specials you can add to the fan duct if you want, but of course these aren't needed. Just read the details for each extra.

### Credits
Thanks to all the awesome Users from my Discord that tested this duct over and over angain. Special thanks to Oldcrazy for all his ideas and mods. Thanks to Thomas for the name.

---

### Limitations
Even though this Duct has a very high range of supported Hotends and extruders, there're still some limitations, due to the design or the time I had spent on this design

#### 1. Fit's only the stock plate
    
##### a) MGN:</dt>
- Oldcrazy from my Discord made a MGN version. Will be uploaded soon - you can get it from my Discord in the meantime.
            
##### b) Non-Ender 3 Printers:
- This Duct resuses the hotend-mounting-standoffs aand the two M3-thread holes on the left where the stock cover is attached to. If your printer doesn't have these you can get a x-plate like the Ender 3 one very cheap in [Ali](aliexpress.com/item/1005001315276573.html?) or with some luck second hand locally.
Please note that eveen the Ender 3 S1 uses a different plate which doesn't have the required holes.

#### 2. No support for Mosquito or mosquito clone

- Aside the fact I want support Slice for [reasons](https://www.reddit.com/r/VORONDesign/comments/rpyqpq/voronslice_beef/), the heaterblock of the Mosquito is just too big, and won't allow any cooling from the front (the duct would be way too far away for any cooling effect). 
        
#### 3. Two side cooling
    
- I already got some requests for a dual 5015 version, which would allow 3 or 4 sided cooling, but in my opionon that would be an overkill. With the speeds we reach with the Ender 3 a single 5015 is more than enough. I want to explain why:
        
##### a) Print speeds:

- I know fast printing got very popular, but even with 300 or 400mm/sec print speed the single 5015 is more than enough. Even though you print with high speeds, external and briging parameters are still kinda slow. We all fo fast on the infill but not for the externals because that results in poor quality and printing tolerances. Less cooling on the infill also means better layer adheasion.
            
##### b) 5015 ≠ 5015:

- There're many brands of 5015 fans out there. When you look for a 5015 on Amazon Winsinn is probably the first result you get. Before you install a dual 5015 with two Winsinn fans, just build a proper single 5015 setup. Winsinn fans are very weak, while Delta or Sunonfans are pretty much the best you can get. Somewhere inbetween are fans by GDstime. In the end you have to pick a fan that fits your requirements. I print ABS only so I don't need much cooling and also use a Winsinn. If you print a lot of PLA you should consider one of the just named brands.

### Changelog:

08.02.2023: Fix of the V6 mounts

05.02.2023: Some fixes:
    
    - ~~5015 holder got an additinal hole to fit the Ender 3 V2 mounting holes~~ That didn't work
    
    - Overhang on the 5015 holder is less steep now, makes printing easier.

11.12.2022: Initial Release

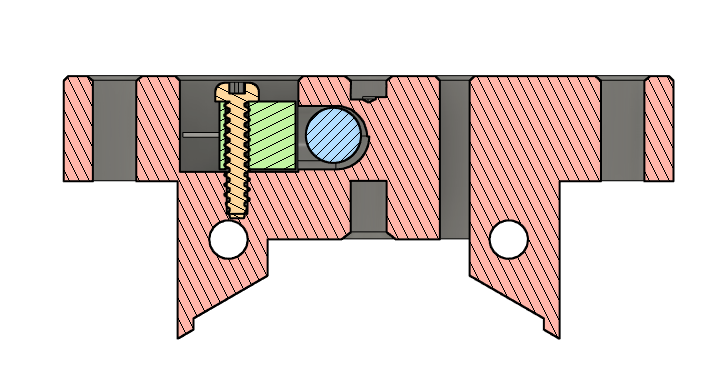
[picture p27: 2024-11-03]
User Mods/adamstorm/Filament Sensor/Images/Section.png

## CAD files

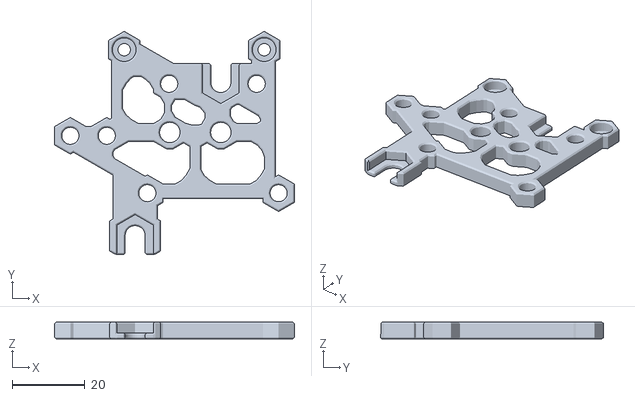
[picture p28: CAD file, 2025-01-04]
STLs/Base/Ender 3 V-wheel Carriage/Beta mount/E3Max/E3Max Plate Mount v1b2.stl
65.8 x 61.2 x 4.60

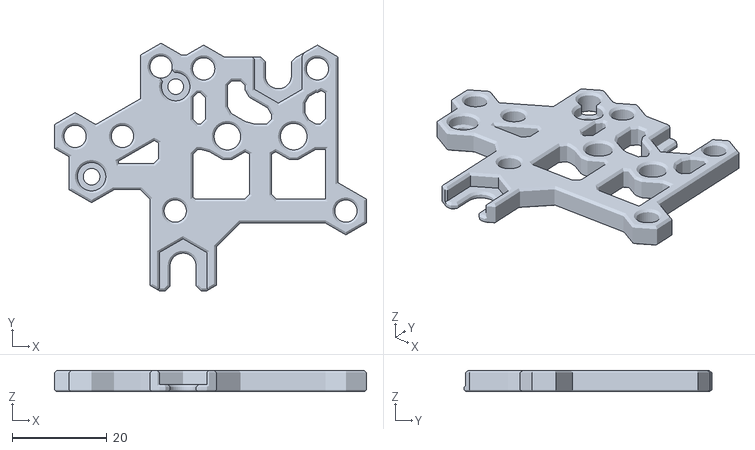
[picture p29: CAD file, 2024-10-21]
STLs/Base/Ender 3 V-wheel Carriage/Beta mount/Plate Mount (extra mount point) v1.0b.stl
65.8 x 52.3 x 4.50

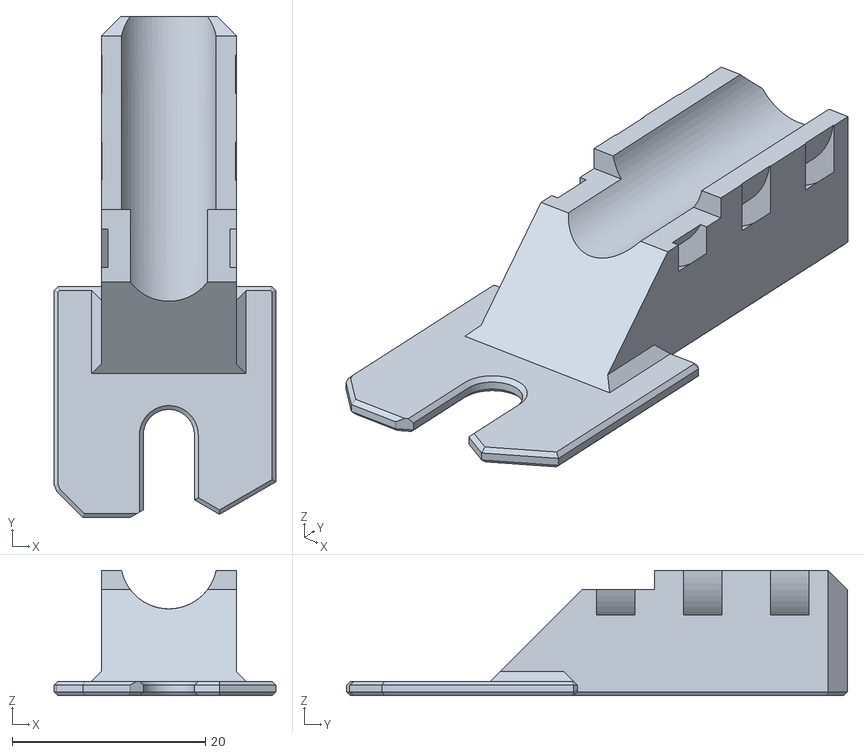
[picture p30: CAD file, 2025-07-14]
STLs/Base/Ender 3 V-wheel Carriage/Cable Mount v1.0.stl
23.0 x 51.9 x 13.0

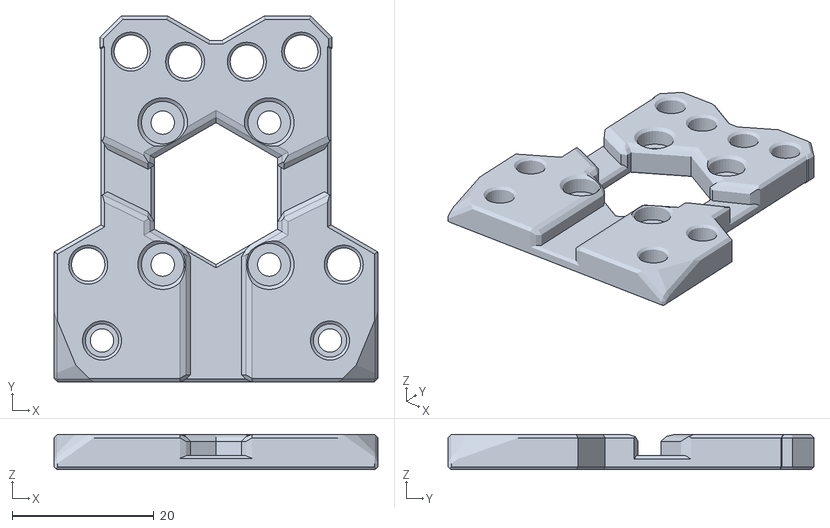
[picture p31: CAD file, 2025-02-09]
STLs/Base/MGN12/Klack Fix Beta/MGN12C Plate v1.01b.stl
45.6 x 51.6 x 5.00

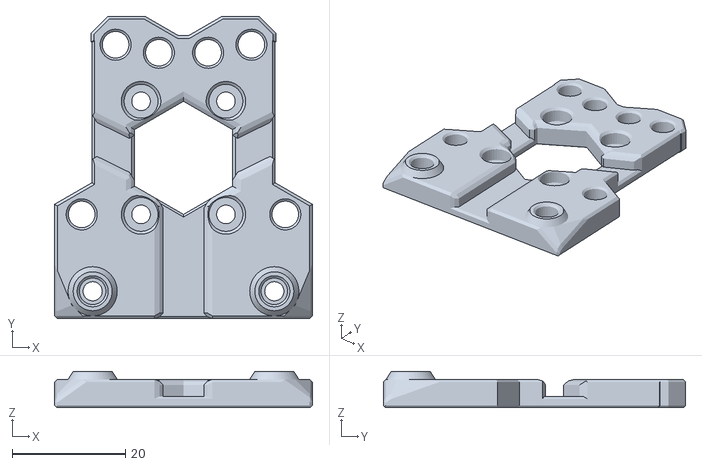
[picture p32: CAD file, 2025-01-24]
STLs/Base/MGN12/MGN12C Plate v1.0.stl
45.6 x 53.5 x 6.40

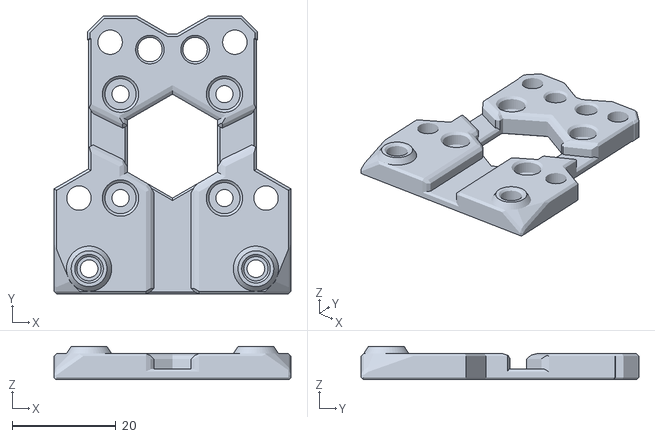
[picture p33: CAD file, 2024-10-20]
STLs/Base/MGN12H/MGN12H Plate v1.0.stl
45.6 x 53.5 x 6.40

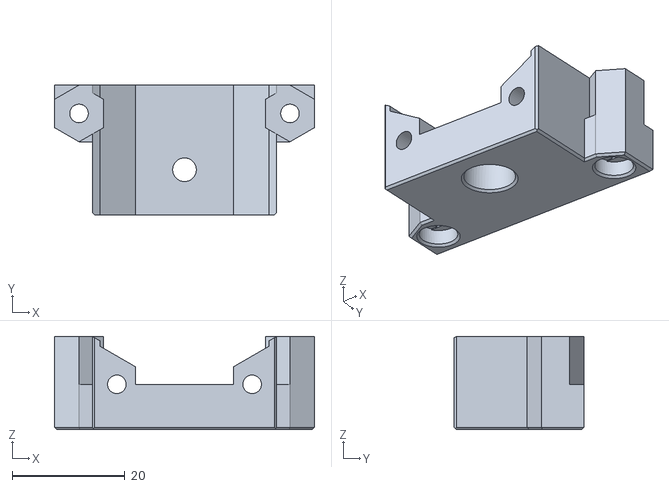
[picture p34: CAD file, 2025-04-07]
STLs/Extruder Mounts/Bowden PC4-M10 (0.125 NPT) v1.0.stl
46.1 x 23.0 x 16.5

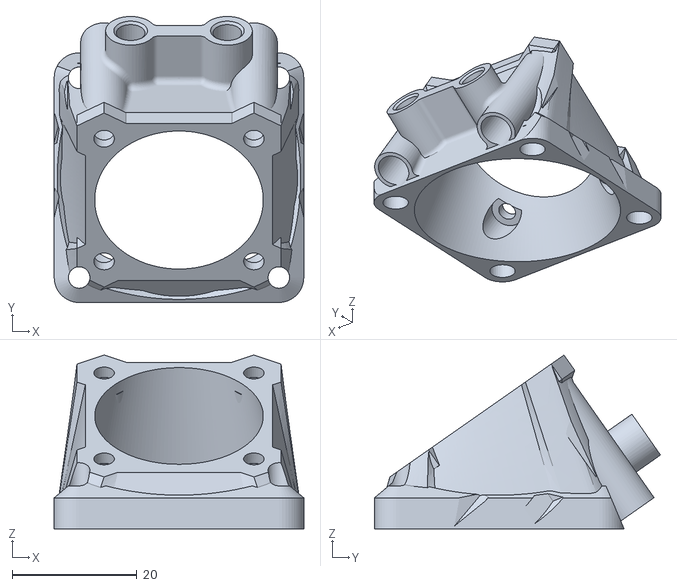
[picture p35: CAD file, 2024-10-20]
STLs/Hotend Mounts/4010_Adapter_ADXL v1.0.stl
40.0 x 45.8 x 27.9

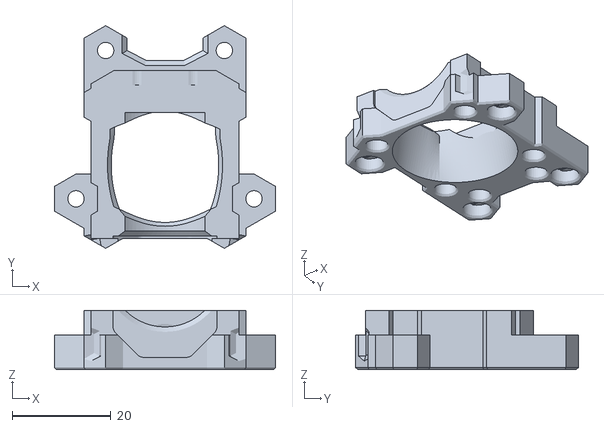
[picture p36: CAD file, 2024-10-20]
STLs/Hotend Mounts/Dragon/Front v1.0.stl
44.7 x 45.0 x 12.0

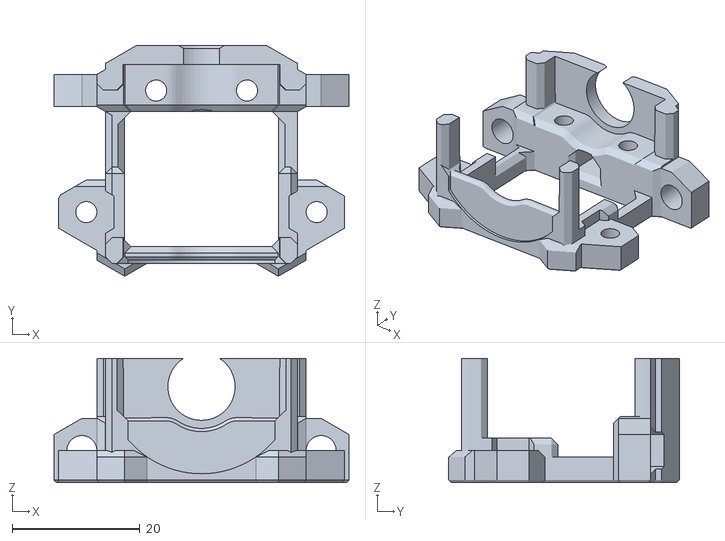
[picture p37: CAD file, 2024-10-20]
STLs/Hotend Mounts/Dragonfly 7 Fin BMS/Back v1.0.stl
46.1 x 36.0 x 19.4

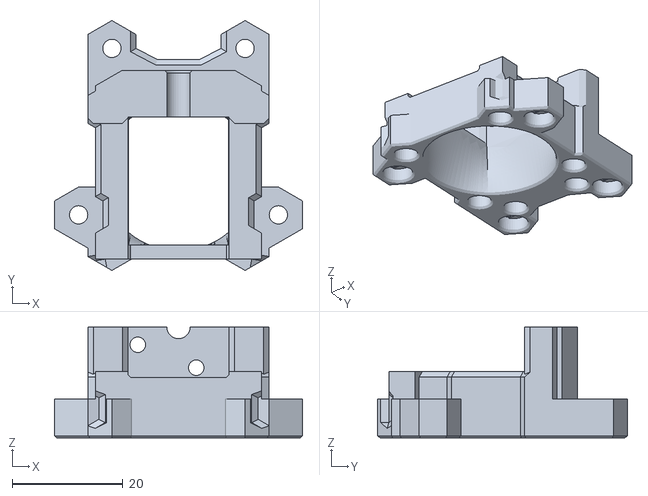
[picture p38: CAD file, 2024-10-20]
STLs/Hotend Mounts/Dragonfly BMO/Front v1.0.stl
44.7 x 45.0 x 20.0

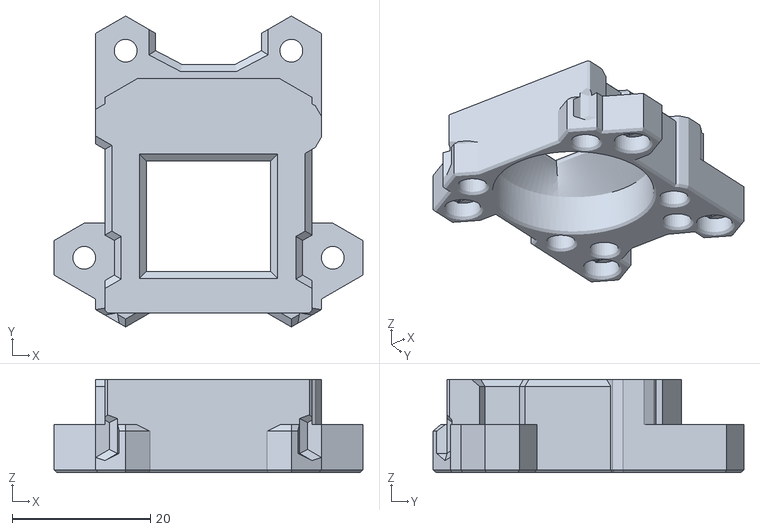
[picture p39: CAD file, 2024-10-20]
STLs/Hotend Mounts/Mosquito/Front v1.0.stl
44.7 x 45.0 x 13.5

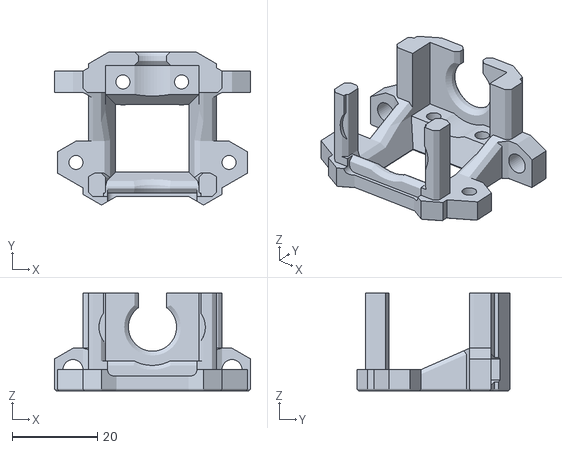
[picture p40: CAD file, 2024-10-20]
STLs/Hotend Mounts/Spider V2/Back v1.0.stl
46.1 x 36.0 x 23.0

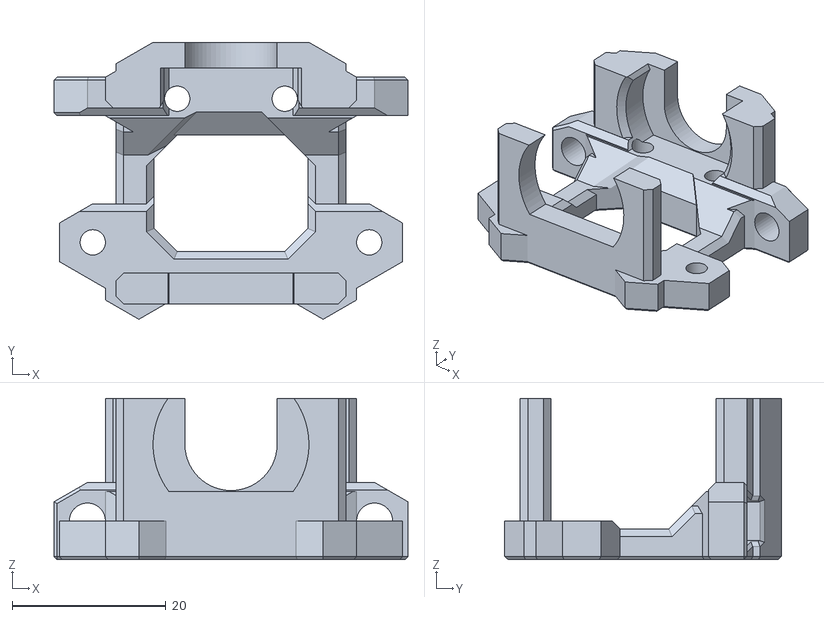
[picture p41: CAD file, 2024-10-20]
STLs/Hotend Mounts/Stock Ender 3/Back v1.0.stl
46.1 x 36.0 x 21.0

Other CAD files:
STLs/Hotend Mounts/Spider Pro/Front v1.0.stl
STLs/Hotend Mounts/Triangle Labs TR6/Back v1.0.stl
STLs/Hotend Mounts/TZ V6/Front v1.01.stl
STLs/Part Cooling/4010/LED Duct Left v1.01.stl
Archive/Archive Frank 1.0/Extras/LED_SK6812/LED_Mount.step
Archive/Archive Frank 1.0/Extras/LED_SK6812/LED_Mount.stl
Archive/Archive Frank 1.0/STL/CommonAll/BL_CR_Touch_mount.3mf
Archive/Archive Frank 1.0/STL/Extruder/Bowden/BMS6/5015Holder.3mf
Archive/Archive Frank 1.0/STL/Extruder/Bowden/BMS7/5015Holder.3mf
Archive/Archive Frank 1.0/STL/Extruder/Bowden/CommonBowden/CableHolder_ZipTie.3mf
Archive/Archive Frank 1.0/STL/Extruder/Bowden/Dragon/5015Holder.3mf
Archive/Archive Frank 1.0/STL/Extruder/Bowden/Dropeffect_XG/5015Holder.3mf
Archive/Archive Frank 1.0/STL/Extruder/Bowden/Revo_Micro/5015Holder.3mf
Archive/Archive Frank 1.0/STL/Extruder/Bowden/Revo_Voron/5015Holder.3mf
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

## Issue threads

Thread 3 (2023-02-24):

Creality Spider Hotend not fitting

RoP09, 2023-02-24:
Hi,

I built the BMS7 version  for the Orbiter v2 ince it says that one can be used for the Spider Hotend.

However I had to make some serious modifications in order to make it fit:
- the upper of the 2 mounting screw holes is not fitting, needs to be placed more up left (at least on my Ender 3 V2 that is)
- the right carriage mounting hole needs to be placed a little more to the right it seems (also maybe related to my Ender 3 V2)
- the spider Hotend is too big, the right side where the BL touch can be attached needed to be cut off by 3mm
- the fan guide is also much too deep for the Spider, had to cut off like 5mm to make it fit.

The upper issues I could correct by drilling a bit, but the one below  could not yet fix easily:
- the orbiter sits too far back if used with the spider hotend, around 3-4mm
-  I have a short PTFE Tube connecting Orbiter and Spider now, but that one is now seriously bent back

The  extruder works but I am uncertain if that bent PTFE tube affects performance as also the filament then has to travel that cruved path.

Some other issues (maybe not supported):
- I use a CR touch, but the mount is much too high if used with the spider hotend. For now 2 M4 hex nuts used as spacers do the job.
- I have a Sunon 5015 fan but the duct is much too tight fitting when the screws are mounted and I broke it easily (not the best way of attaching, maybe that could be enforced? For now I simply glued the whole duct directly to the fan which works fine it seems.

Besides that I really like the FrankEnstein-Duct :)

nurglexp, 2023-03-01:
I'd really like to use Frank with my E3v2 and Creality Spider 500oC. Any plans to support it if the BMS7 version doesn't fit?

Closed 2024-10-20.

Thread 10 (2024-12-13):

Further improve 5015 duct interference

wight554, 2024-12-13:
While trimming hotend mount here kinda works, it's still a bit too tight here , especially with shrinkable materials
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

I'd recommend trimming 5015 holder a little so there's nice clearance between hotend mount and 5015 holder, like this:
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

Step file:
[5015_Holders (1).step.zip](https://github.com/user-attachments/files/18124508/5015_Holders.1.step.zip)

hawk16zz, 2025-01-04:
Tot a fan of trimming them as they are made nessle in that groove in the mounts, but I will add a little clearance (I think 0.1mm should be plenty) as they are flush right now and that should improve the fitment enough.

Closed 2025-01-04.

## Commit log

2022-11-27 Initial Release
    Initial Release of FrankEnstein
    [5015Holder.3mf, 5015Holder_Clamp.3mf, BL_Touch_mount.3mf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]
2022-12-11 LGX Lite and TBG Lite fix
    The holders for the LGX Lite and the TBG Lite collided with the 5015 holder. This has been fixed.
    [BMS7_TGB_Mount.3mf, BMS_LGX_LiteMount v1.3mf, BMS_TGB_Mount.3mf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]
2023-02-05 5015 fixes
    see changelog
    [5015Holder.3mf]
2023-02-08 V6 fix
    [5015Holder.3mf]
2023-05-01 Fix Sherpa Mini Cable Holder
    [BL_CR_Touch_mount.3mf, BL_Touch_mount.3mf, CableHolder_ZipTie.3mf]
2023-06-24 Frank2.0 Beta Start
    [4010Holder_Left.stl, 4010Holder_Right.stl, 4010_Adapter.stl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]
2023-06-26 Update + BMS7
    [4010Holder_Left.stl, 4010Holder_Right.stl, 4010_Adapter.stl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]
2023-06-26 BMS7 Note
2023-07-02 Frank 2.0 BETA Update
    [Back.stl, Front.stl]
2023-07-02 BETA BOM
2023-07-03 BETA CAD
2023-07-05 BETA Update
    [4010_Adapter.stl, BLTouchMount.stl, Back.stl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]
2023-07-05 I forgot the CAD... again
2023-07-07 Aaaand the CAD
2023-07-09 Overhang fix
    [Back.stl]
2023-08-24 CAD Update + minor wire fix on the 5015 LEDs
    [LED_5015Duct_Left.stl, LED_5015Duct_Right.stl]
2024-10-20 Frank v2 v1
    Finally here v1 of v2. Everything's moving around. OG v1 and v2 beta move to archive folders
    [4010 Holder Left v1.0.stl, 4010 Holder Right v1.0.stl, 4010 spacer (group of 4) v1.0.stl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]
2024-10-21 Create Plate Mount (extra mount point) v1.0.stl
    Added plate mount with point for the bottom v wheel attachment
    [Plate Mount (extra mount point) v1.0.stl]
2024-10-22 TZ V6 correction
    Fixed a pair of chamfers and a height difference between the front and back. Also added versions for use with V6 nozzles (I hate these naming schemes). V1.0 moved to Old
    [Back (V6) v1.01.stl, Back v1.0.stl, Back v1.01.stl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]
2024-10-22 Klack
    Forgot to upload the klack holder for linear rail, oops
    [Klack Mount v1.0.stl]
2024-10-22 Fixes of the missing
    Fixed more missing chamfers and adjusted MGN12H picture
    [MGN12H Plate v1.0.stl, MGN12H Plate v1.01.stl]
2024-10-25 Correct belt holder
    Accidently uploaded an older version of the belt holder, here's the correct one.
    [Belt Holder v1.0.stl, Belt Holder v1.01.stl]
2024-10-27 file names
    [Back (for V6 nozzle, UNTESTED) v1.01.stl, Front (for V6 nozzle, UNTESTED) v1.01.stl]
2024-11-01 Added CAD and STLs
    [Frank 2.0 Filament Sensor.step, Frank 2.0 Filament Sensor.stl]
2024-11-01 Title Cleanup
    [Frank 2.0 Filament Sensor.step, Frank 2.0 Filament Sensor.stl]
2024-11-03 The LED Duct Fix
    Removed dummy LEDs from the duct as they will not shed light
    [Back v1.0.stl, Belt Holder v1.0.stl, Front v1.0.stl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]
2024-11-10 Create Camera Mount User Mod
    [Adapter Plate.stl, Camera Holder.stl, Frank2.0 Endoscope Camera Mount.f3d]
2024-11-10 Added Camera Mount to User Mod list
2024-12-13 Add a bunch of my mods
    [Dragon_2510.step, Dragon_2510_Back.stl, Dragon_2510_Front.stl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]
2024-12-14 Add a bunch of my other mods
    [Klack_HF.step, Klack_HF_Dock.stl, Klack_HF_Mount.stl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]
2024-12-17 Add my mods to main readme and fix klack uhf stuff
    [Klack_HF.step, Klack_HF_Dock.stl, Klack_HF_Mount.stl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]
2025-01-04 5015 holders clearance fix...
    [5015 Holder Left v1.0.stl, 5015 Holder Left v1.01.stl, 5015 Holder Right v1.0.stl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]
2025-01-04 E3Max Beta Plate revision
    [E3Max Plate Mount v1.b1.stl, E3Max Plate Mount v1b2.stl]
2025-01-24 Added MGN12C base
    [Belt Clip v1.0.stl, Belt Holder v1.0.stl, Belt Holder v1.01.stl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]
2025-02-04 Update README.md
    A little BoM cleanup
2025-02-09 beta fix for klack docking
    [Belt Holder v1.02b.stl, MGN12C Plate v1.01b.stl, MGN12H Plate v1.02b.stl]
2025-02-09 klack fix beta for real this time
    [Belt Holder v1.02b.stl, MGN12C Plate v1.01b.stl, MGN12H Plate v1.02b.stl]
2025-02-28 Add extruder mount for Creality Sprite Extruder (#14)
    * Added Sprite Extruder Mount
    * Update README.md
    [Frank 2.0 Sprite Extruder Mount.step, Frank 2.0 Sprite Extruder Mount.stl]
2025-04-07 The CAD Update
    Long awaited CAD update and ECAS and PC4 mounts
    [Bowden ECAS v1.0.stl, Bowden PC4-M10 (0.125 NPT) v1.0.stl]
2025-05-19 n4t3y - USERMOD - 5015 AIO Ducts (#15)
    * Create README.md
    * Create README.md
    * Create README.md
    * Create README.md
    * Create README.md
    * Create README.md
    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
    [5015 AIO Duct Bracket.stl, 5015 AIO Duct.f3d, 5015 AIO Duct.stl]
2025-06-17 Updated AIO Duct files and added LED AIO Duct (#16)
    * Many README.md edits
    * Much Add files via upload
    * Delete User Mods/n4t3y/AIO 5015 UHF Duct directory
    * Rename Screenshot 2025-05-20 090937.png to Assembled.png
    * Rename Screenshot 2025-05-20 091240.png to MountandDuct.png
    * Rename Screenshot 2025-05-20 091400.png to Bracket.png
    * Rename Screenshot 2025-05-20 091457.png to MountwBracket.png
    * Rename Screenshot 2025-05-20 093033.png to RHSAIOMount.png
    * Rename Screenshot 2025-05-20 093113.png to RHSOriginalHolder.png
    * Rename Screenshot 2025-06-17 135135.png to LED_Assembled.png
    * Updated file for TZ mount
    Thinner bolt hole to fix clash with TZ heatsink - also compatible with ot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
    [5015 AIO Duct Bracket.stl, 5015 AIO Duct v2.f3d, 5015 AIO Duct v2.stl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]
2025-06-17 Updated Readme with LED Duct link (#17)
    ---------
    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
2025-07-14 Create Cable Mount v1.0.stl
    Zip tie mount for v-wheels
    [Cable Mount v1.0.stl]
2025-07-24 Further archive the archives
    [4010Holder_Left.stl, 4010Holder_Right.stl, 4010_Adapter.stl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]
2026-01-28 Fan letters
    Added L and R indicators to the 4010 ducts
